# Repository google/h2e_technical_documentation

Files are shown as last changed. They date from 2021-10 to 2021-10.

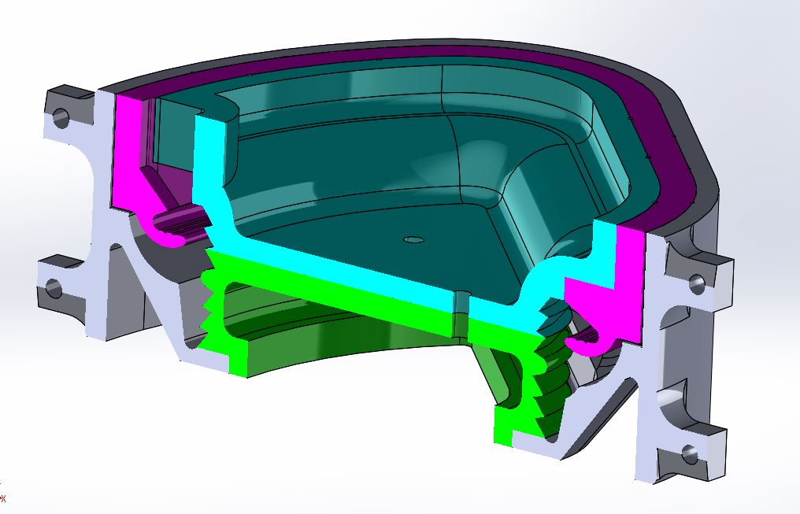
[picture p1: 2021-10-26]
CAD_files/P4-Grommets/P4-Pie-Shaped-Grommet/CrossSectionGromPieMold.JPG

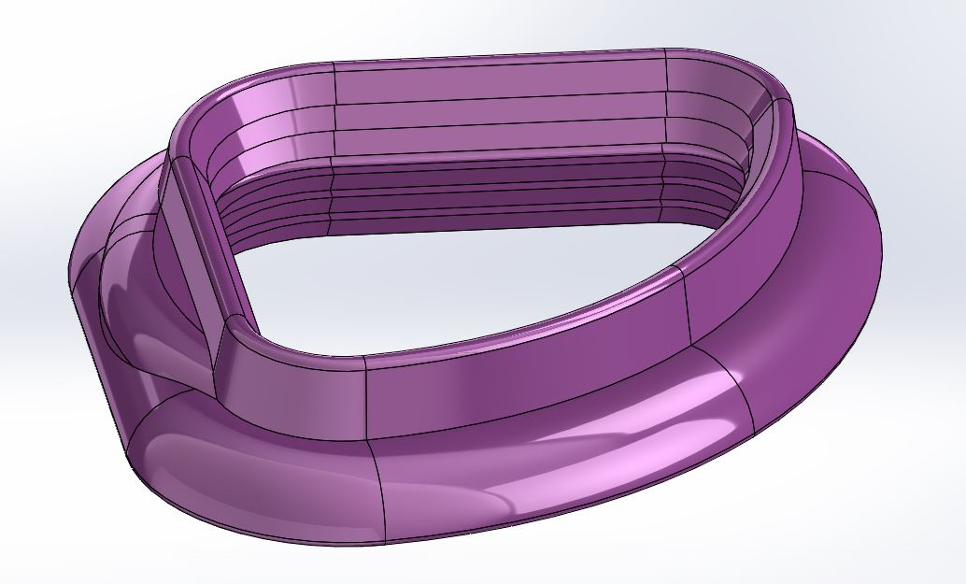
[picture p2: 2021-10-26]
CAD_files/P4-Grommets/P4-Pie-Shaped-Grommet/GromPie.JPG

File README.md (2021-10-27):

# H2E Technical Documentation Set

Summary:  
Over 2 billion people do not have access to safe drinking water. H2E was a 
project at X that aimed to tackle this challenge by creating a device that 
individual households could use to harvest water from the air. The team aimed 
to build a highly lightweight, portable, cheap (\<5% of user’s income) device 
that an individual could use to produce 5L of drinking water per day.

This is no longer an active project at X, so we are releasing our technical 
documents to allow others to build on our progress to date. To do so, we have 
made the following items public:

* [Nature paper](https://www.nature.com/articles/s41586-021-03900-w) with key 
findings
* Tools/code that enabled findings shared in the paper, and others in the AWH 
community can use, including:
    * “AWH-Geo” which can estimate the water output over time of any AWH 
    device. This can then be used to estimate the potential user base and 
    impact of an AWH device. On 
    [GitHub](https://github.com/AWH-GlobalPotential-X/AWH-Geo)
    * “JMP GeoProcessor” which uses geographic information systems (GIS) to 
    process the UNICEF/WHO data and join them to proper geographic boundaries. 
    In [FigShare](https://figshare.com/projects/AWH-GlobalPotential-X/96476) 
    * Much of the data analysis code used to produce the figures & charts in 
    the study. On [GitHub](https://github.com/AWH-GlobalPotential-X/AWH-Geo) 
* Two datasets on 
[FigShare](https://figshare.com/projects/AWH-GlobalPotential-X/96476) 
* Hardware assembly documentation
    * CAD files of our prototype device: These can be found in the folder 
    called “CAD_files” 
    * “Assembly_documentation.pdf”, this document details our prototype
    assembly process and learnings
* [Patent Non-Assertion Pledge ](https://storage.googleapis.com/x-prod.appspot.com/files/H2E%20Patent%20Non-Assertion%20Pledge.pdf)

Data and geospatial tools around access to safe drinking water are provided 
here to aid academic reproducibility and advancement in the context of the 
Nature Paper “Global Potential of Harvesting Drinking Water from Air using 
Solar Energy”. They should not be used for decision making without extensive 
validation. This caveat applies even more strongly outside the field of 
atmospheric water generation, where assumptions and approximations made may not 
be suitable . Users are encouraged to use the official public sources 
(primarily WHO/UNICEF JMP) from which they are derived.

Data and results capture a snapshot at the time of research, and are compiled 
at the time of publication (2021-10-27). They will not be updated, even as 
underlying realities change.

The prototype described here is a purely experimental device. While 
substitutions and modifications are reasonably straightforward, water harvested 
with this experimental device is not intended to be ingested. Among other design choices, adhesives were selected for experimental performance and would need to be substitued with ones meeting food grade standards. 

The views expressed in the paper and co-released documentation are the 
author’s, and not necessarily the views of authors’ employers.

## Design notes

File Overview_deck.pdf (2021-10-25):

Confidential & Proprietary

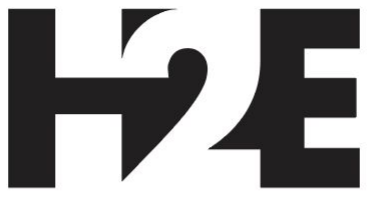
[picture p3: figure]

# Hydration to Everyone

Providing clean drinking water to every household without the need of treatment or transportation

# Problem: 2 bn people lack access to safe & reliable drinking water

## Safety

Diarrheal diseases due to unsafe drinking water is responsible for approximately 485,000 deaths a year¹

WHO estimates that it will take $203 billion in infrastructure investment to provide piped water to people currently underserved⁶

## Affordability

Water access is often far from the home; women and girls spend 200 million hours daily collecting water for their homes²

## Accessibility

# Solution: Atmospheric Water Harvesting

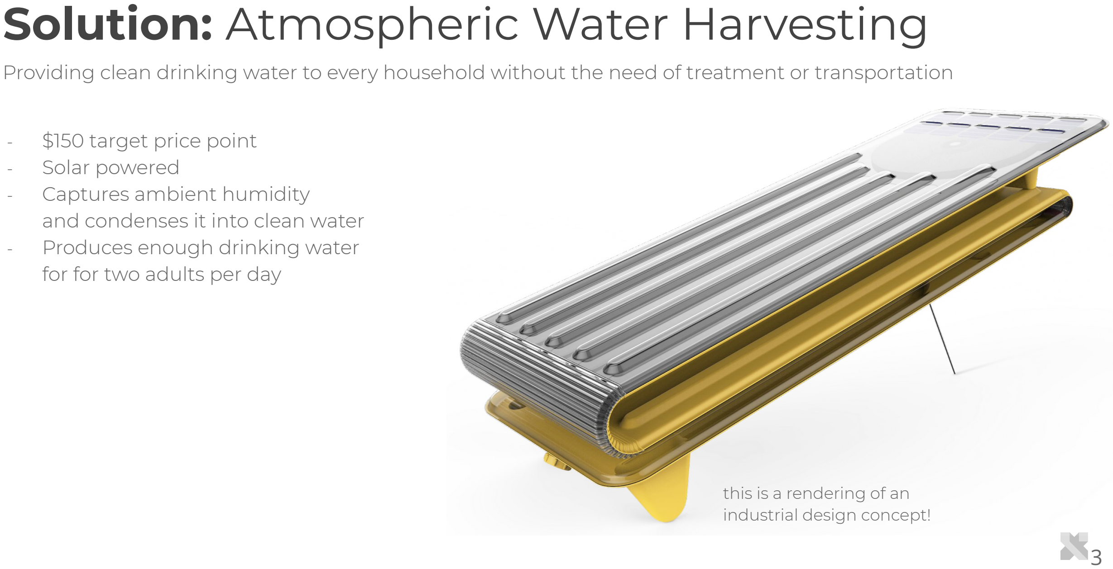
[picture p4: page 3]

### - $150 target price point - Solar powered - Captures ambient humidity and condenses it into clean water - Produces enough drinking water for for two adults per day

Providing clean drinking water to every household without the need of treatment or transportation

this is a rendering of an
industrial design concept!

## 1. Heating

## H2E’s Vacuum Formed Prototype

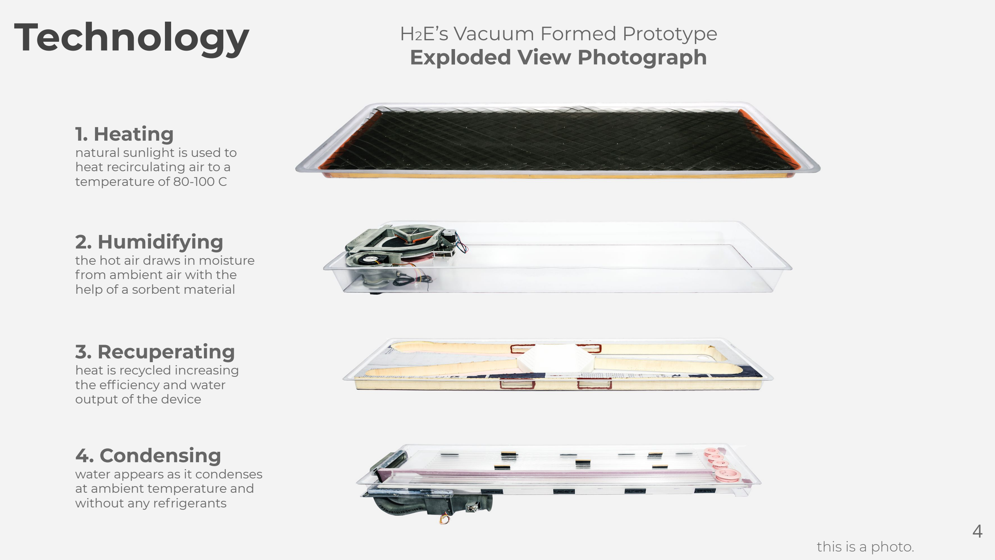
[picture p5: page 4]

natural sunlight is used to heat recirculating air to a temperature of 80-100 C

## Exploded View Photograph

## 2. Humidifying

the hot air draws in moisture from ambient air with the
help of a sorbent material

## 3. Recuperating

heat is recycled increasing the efficiency and water
output of the device

## 4. Condensing

water appears as it condenses at ambient temperature and without any refrigerants

this is a photo.

# Technology

# Air-Flow Path: Humidity supply

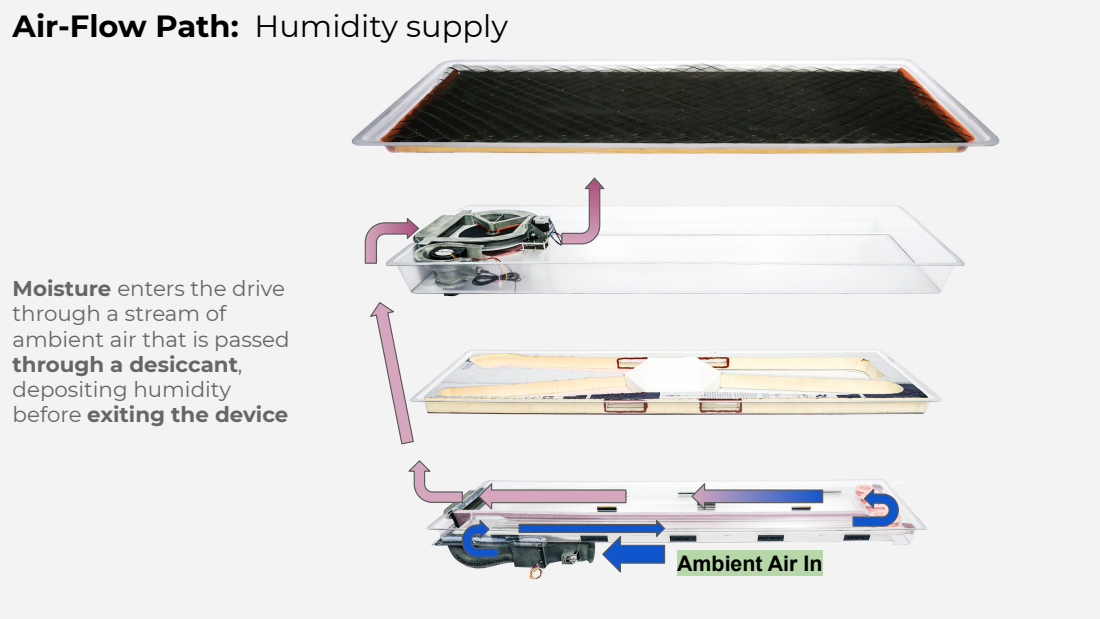
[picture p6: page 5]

Moisture enters the drive
through a stream of
ambient air that is passed
through a desiccant,
depositing humidity
before exiting the device

Ambient Air In

# Air-Flow Path: Recirculated Stream

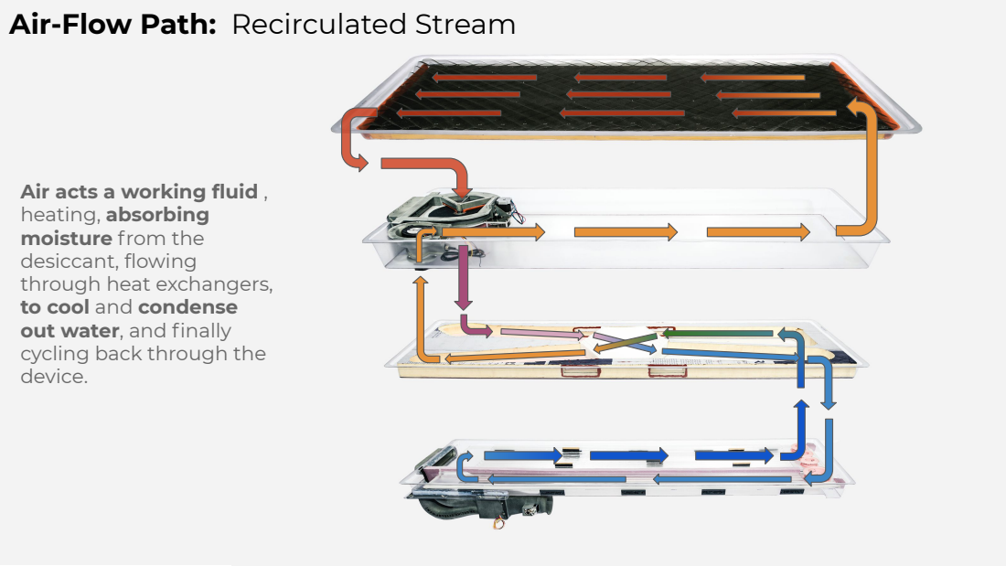
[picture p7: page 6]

Air acts a working fluid ,
heating, absorbing
moisture from the
desiccant, flowing
through heat exchangers,
to cool and condense
out water, and finally
cycling back through the
device.

# Photo of Appearance Mock without the Experimental Gear

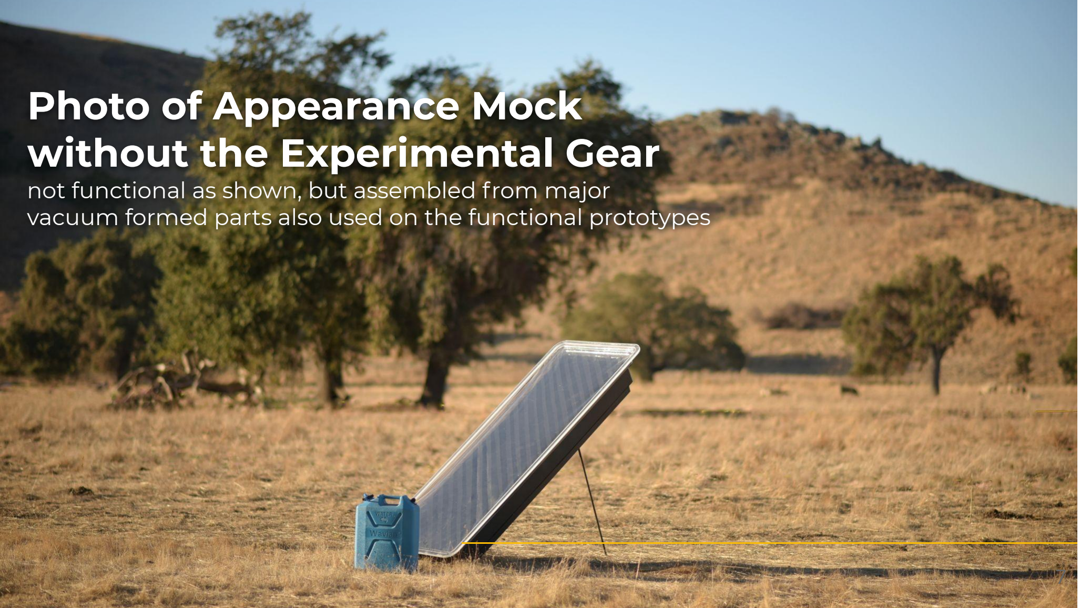
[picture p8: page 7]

## not functional as shown, but assembled from major vacuum formed parts also used on the functional prototypes

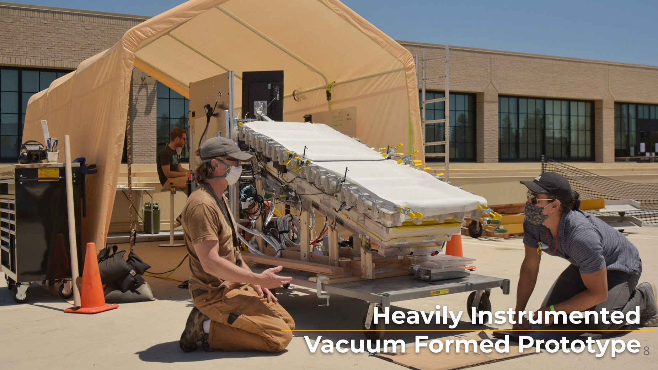
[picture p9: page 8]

# Heavily Instrumented Vacuum Formed Prototype

# Outdoor Experimental Results 2020

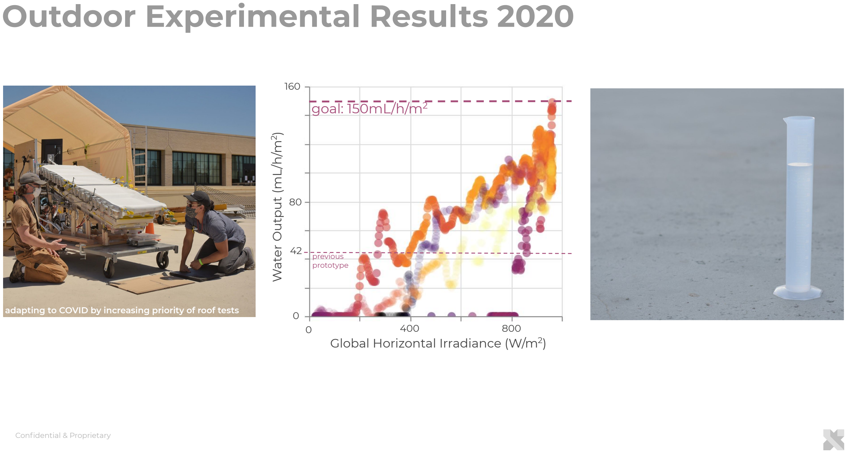
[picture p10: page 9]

Global Horizontal Irradiance (W/m² )

adapting to COVID by increasing priority of roof tests

previous
prototype

Water Output (mL/h/m2

)

42

0

160

80

0 | 400 | 800

goal: 150mL/h/m²

# Device Losses of an AWH

## Approximate Sankey Diagram of

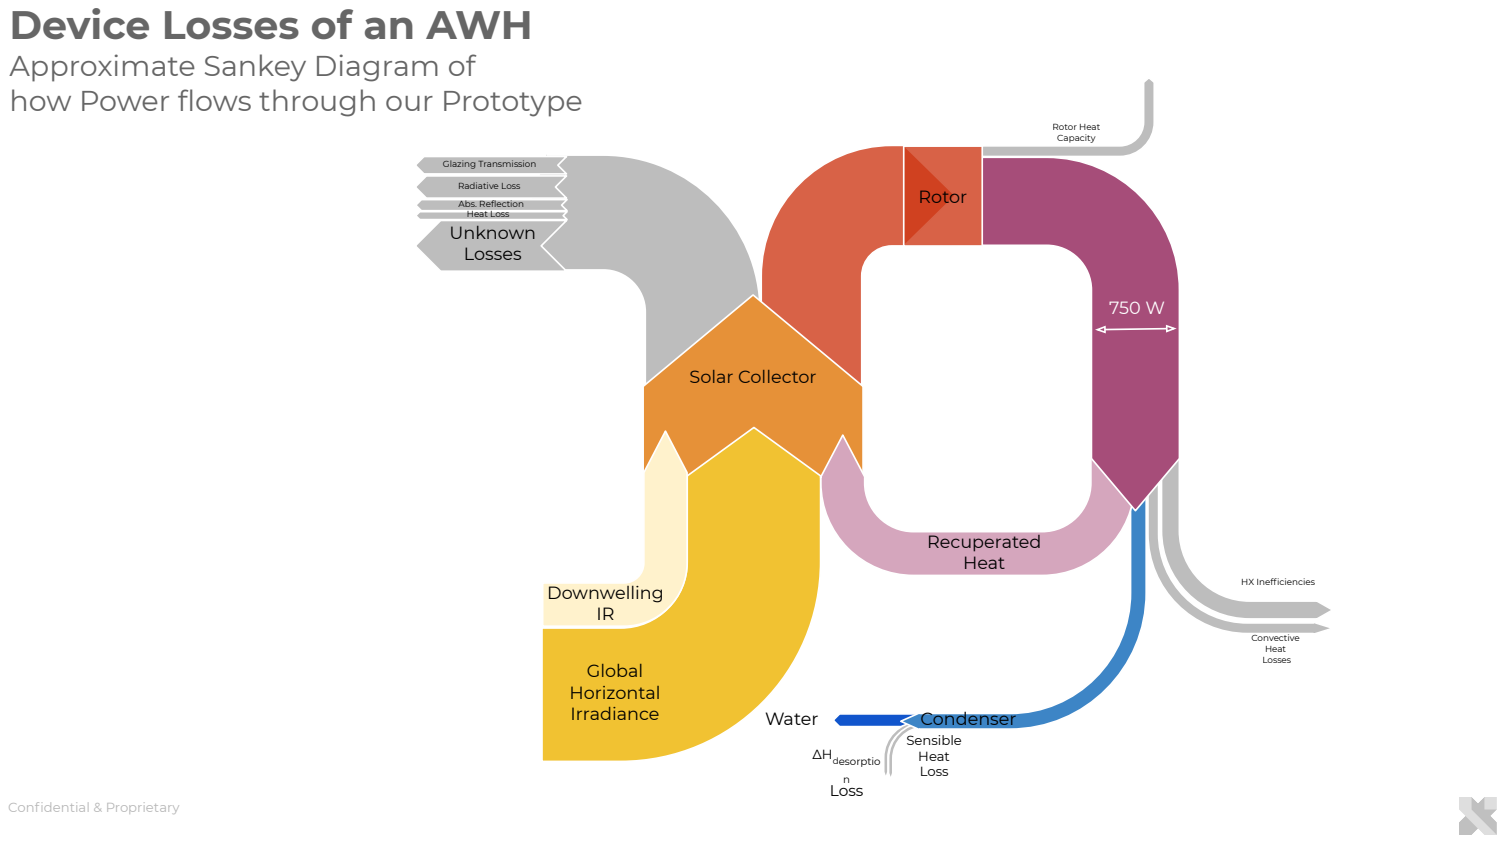
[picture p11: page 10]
Unknown Losses; Glazing Transmission; Radiative Loss; Abs. Reflection Heat Loss; Rotor; HX Inefficiencies; Convective Heat Losses; Water; Sensible Heat Loss; ∆Hdesorptio; n Loss; Condenser; Solar Collector; Global Horizontal Irradiance; Downwelling IR; Recuperated Heat; Rotor Heat Capacity

how Power flows through our Prototype

# Atmospheric Water Harvesting performs best where it is needed most

# Market

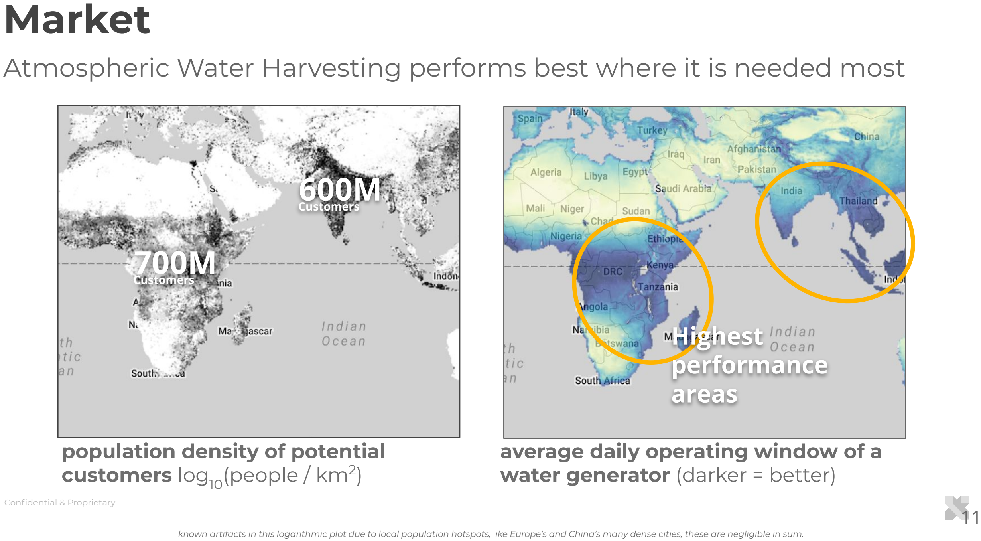
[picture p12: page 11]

known artifacts in this logarithmic plot due to local population hotspots, ike Europe’s and China’s many dense cities; these are negligible in sum.

## population density of potential customers log10(people / km²

)

## average daily operating window of a water generator (darker = better)

Customers

700M

Customers

600M

# Highest performance areas

# How AWH compares to other technologies

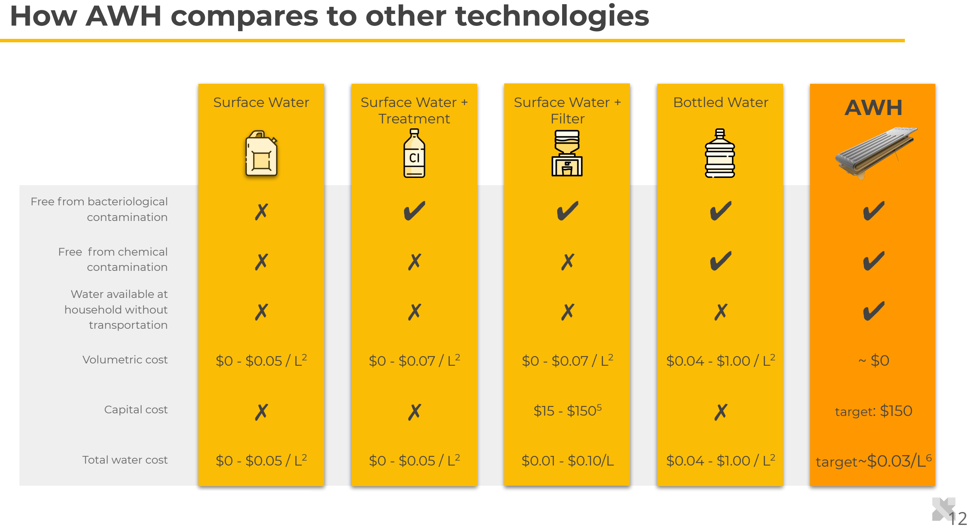
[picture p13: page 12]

Surface Water | Surface Water +
Treatment

Surface Water +
Filter
Bottled Water | AWH

Free from bacteriological
contamination | ✗ | ✔ | ✔ | ✔ | ✔

Free from chemical
contamination | ✗ | ✗ | ✗ | ✔ | ✔

Water available at
household without
transportation | ✗ | ✗ | ✗ | ✗ | ✔
Volumetric cost | $0 - $0.05 / L² | $0 - $0.07 / L² | $0 - $0.07 / L² | $0.04 - $1.00 / L² | ~ $0
Capital cost | ✗ | ✗ | $15 - $150⁵ | ✗ | target: $150
Total water cost | $0 - $0.05 / L² | $0 - $0.05 / L² | $0.01 - $0.10/L | $0.04 - $1.00 / L²

### target~$0.03/L⁶

# References

Page 9

1) Progress on household drinking water, sanitation and hygiene 2000-2017. Special focus on inequalities. New York: United Nations Children’s Fund (UNICEF) and World Health Organization, 2019.
2) Cook, J., P. Kimuyu, and D. Whittington (2016), The costs of coping with poor water supply in rural Kenya, Water Resources Research, 52, 841–859, doi:10.1002/2015WR017468.
3) End-User Preferences for and Performance of Competing POU Water Treatment Technologies among the Rural Poor of Kenya Jeff Albert, Jill Luoto, and David Levine Environmental Science & Technology 2010 44 (12), 4426-4432 DOI: 10.1021/es1000566
4) Low-end range: M. Dzodzomenyo, G. Fink, W. Dotse-Gborgbortsi, N. Wardrop, G. Aryeetey, N. Coleman, A. Hill, J. Wright; Sachet water quality and product registration: a cross-sectional study in Accra, Ghana. J Water Health 1 August 2018; 16 (4): 646–656. doi: https://doi.org/10.2166/wh.2018.055, High end: Data analysis from Ghana Living Standard Survey (GLSS7) 2017
5) PATH, Commercial approaches to delivering household water treatment and safe storage products and solutions to low-income households. Report 2012 https://path.azureedge.net/media/documents/TS_swp_perspectives_rpt.pdf
6) *Assuming 1500 L/yr x 3 yr and remineralization and/or chlorination for residual protection

Page 2
1) Prüss-Ustün A, Wolf J, Bartram J, et al. Burden of disease from inadequate water, sanitation and hygiene for selected adverse health outcomes: An updated analysis with a focus on low- and middle-income countries. Int J Hyg Environ Health. 2019;222(5):765-777. doi:10.1016/j.ijheh.2019.05.004
2) Collecting water is often a colossal waste of time for women and girls. UNICEF. (2021, October 15). Retrieved October 22, 2021, from
https://www.unicef.org/press-releases/unicef-collecting-water-often-colossal-waste-time-women-and-girls.
3) Hutton, Guy, Haller, Laurence & World Health Organization. Water, Sanitation and Health Team. ( 2004) . Evaluation of the costs and benefits of water and sanitation improvements at the global level / Guy Hutton and Laurence Haller. World Health Organization. https://apps.who.int/iris/handle/10665/68568

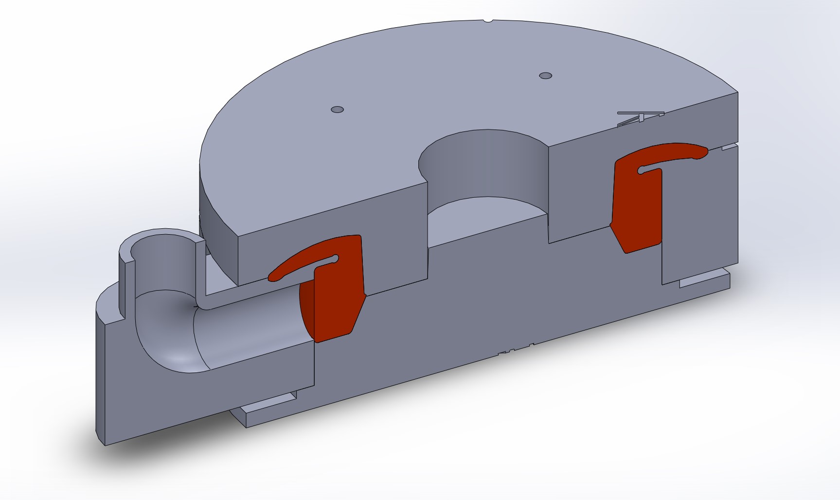
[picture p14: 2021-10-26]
CAD_files/P4-Grommets/Fan Grommet Mold.jpg

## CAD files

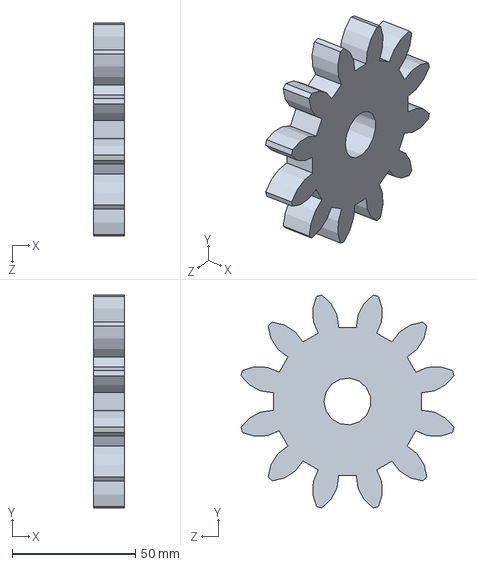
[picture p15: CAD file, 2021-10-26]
CAD_files/Complete P4 Full Assembly/P4_Full/spur gear_ai_P4Full.sldprt
12.7 x 86.4 x 86.4 mm

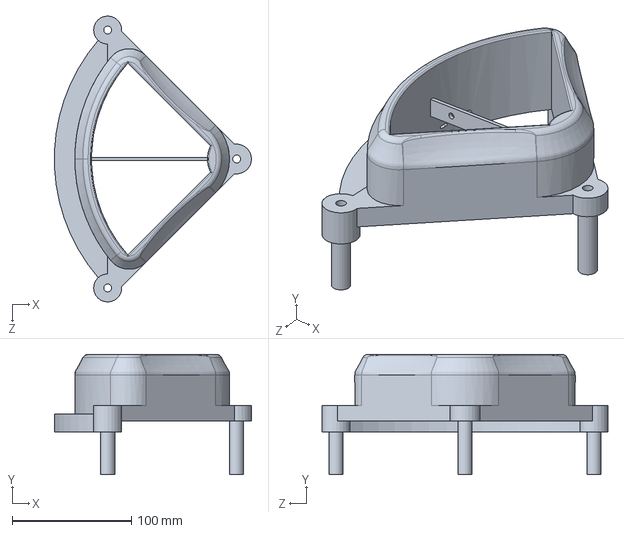
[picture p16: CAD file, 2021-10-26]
CAD_files/Complete P4 Full Assembly/P4_Full/BBP4_PiePieceBottom_P4Full.SLDPRT
165.3 x 101.0 x 240.0 mm

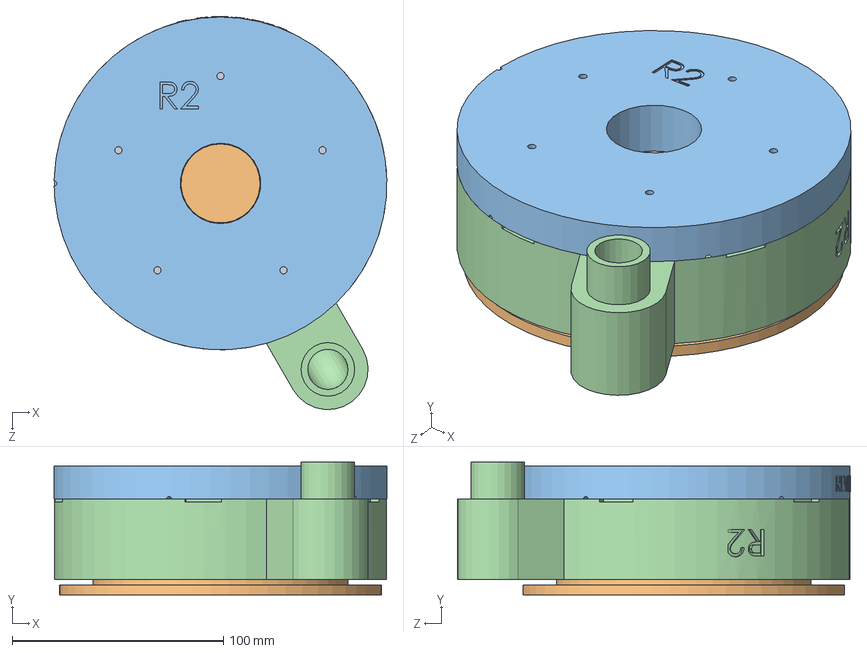
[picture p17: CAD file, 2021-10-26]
CAD_files/P4-Grommets/Fan Gromet Mold/Vent fan mold.SLDASM
157.4 x 62.8 x 186.0 mm
FAN grommet 2
Lower Core_fan_gromet_mold
Mold Lid
Mold Fan Grommet Lower Exterior

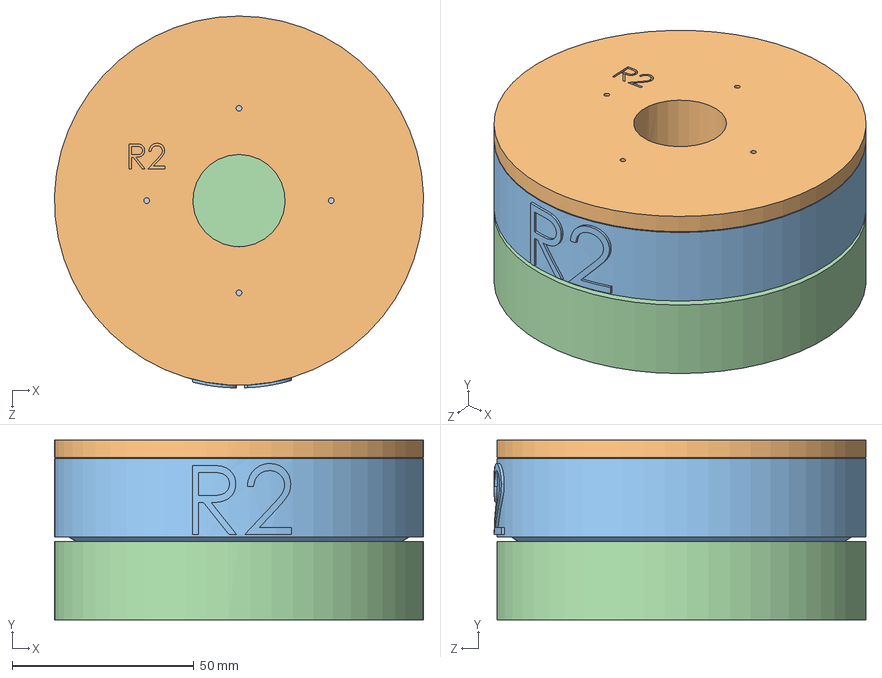
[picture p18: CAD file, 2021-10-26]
CAD_files/P4-Grommets/Gromzilla mold small port/Small port mold.SLDASM
101.6 x 49.5 x 102.4 mm
Rubber Port Tube
MoldHALF_A_small port
Center mold Small port
pass through mold Bottom side

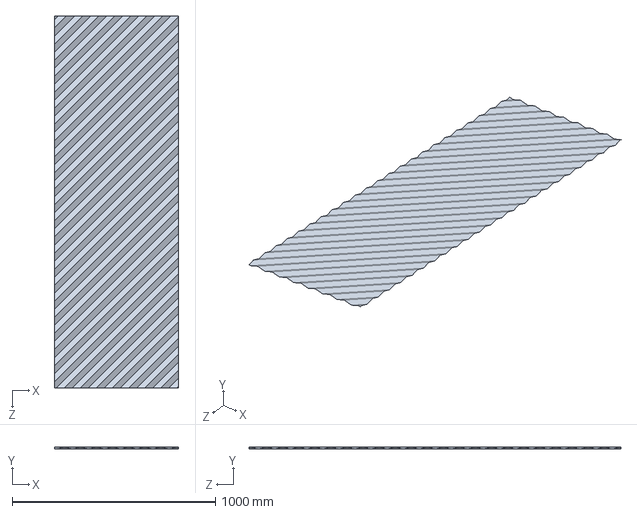
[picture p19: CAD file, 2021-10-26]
CAD_files/Complete P4 Full Assembly/P4_Full/T1 Sol Coat Mesh_P4Full.SLDPRT
609.6 x 11.2 x 1828.8 mm

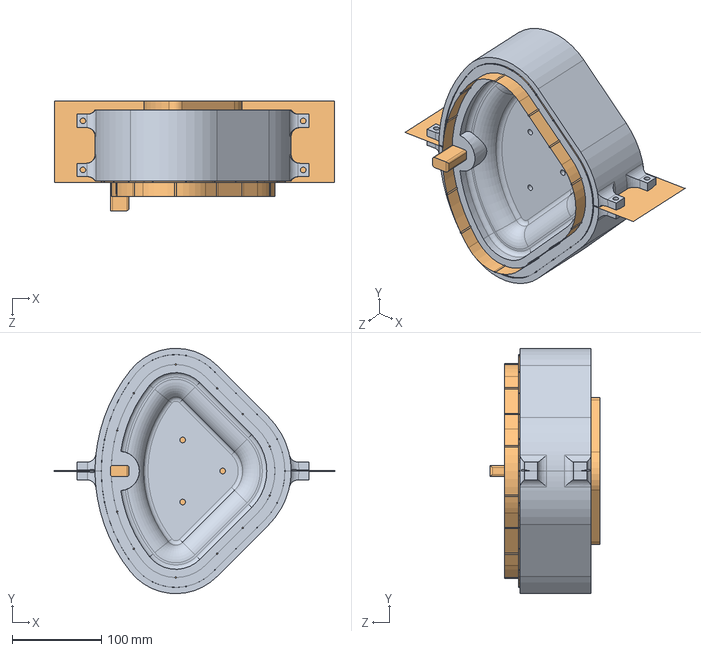
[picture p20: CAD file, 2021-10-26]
CAD_files/P4-Grommets/P4-Pie-Shaped-Grommet/P4-Pie-Shaped-Grommet/A_gromzillaP4MoldV2.SLDASM
314.0 x 275.1 x 122.8 mm
gromzillaP4MoldV2BodyV2
PosMold_GromzilPieV2

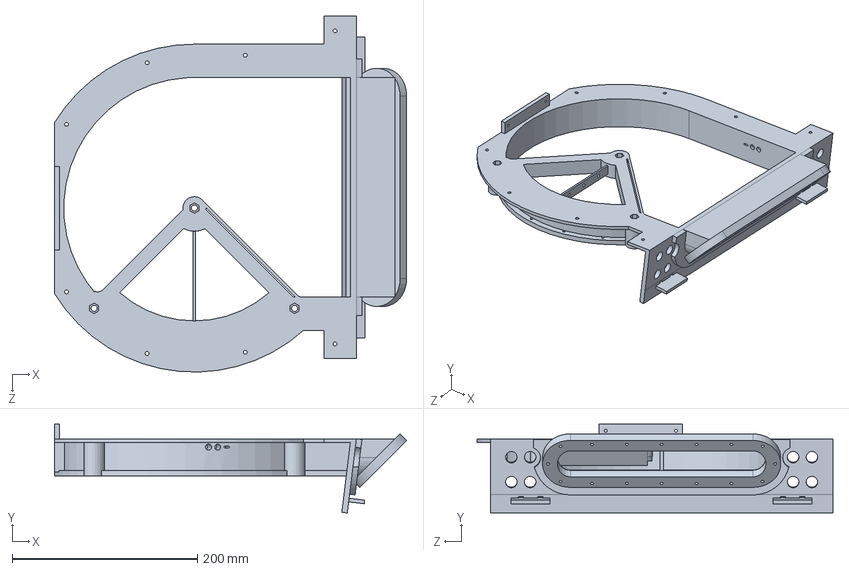
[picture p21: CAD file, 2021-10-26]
CAD_files/Complete P4 Full Assembly/P4_Full/BBP4_Shroud_Angle_For_FlowOp_P4Full.SLDPRT
380.3 x 96.1 x 384.3 mm

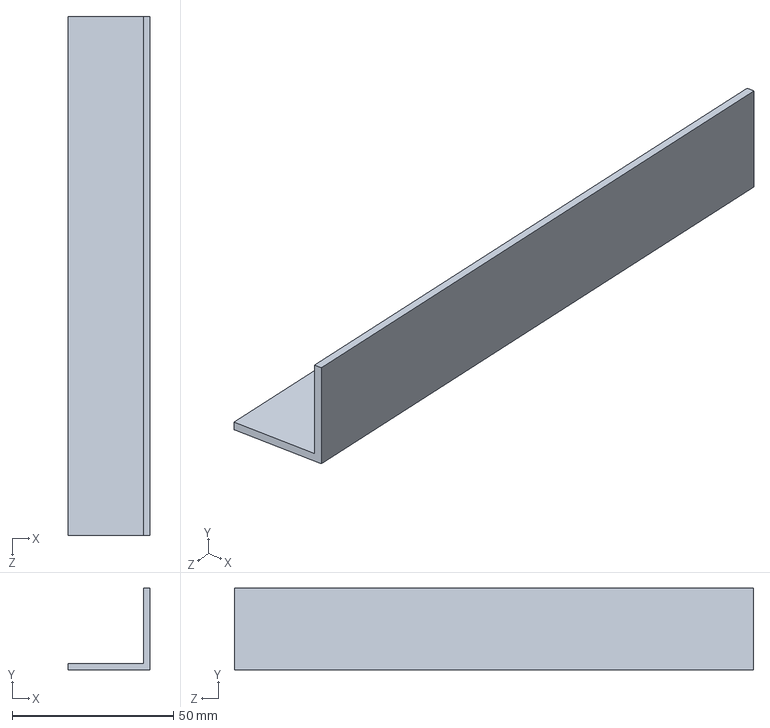
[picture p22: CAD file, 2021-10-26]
CAD_files/Complete P4 Full Assembly/P4_Full/Plastic Ell 1_P4Full.SLDPRT
25.4 x 25.4 x 161.0 mm

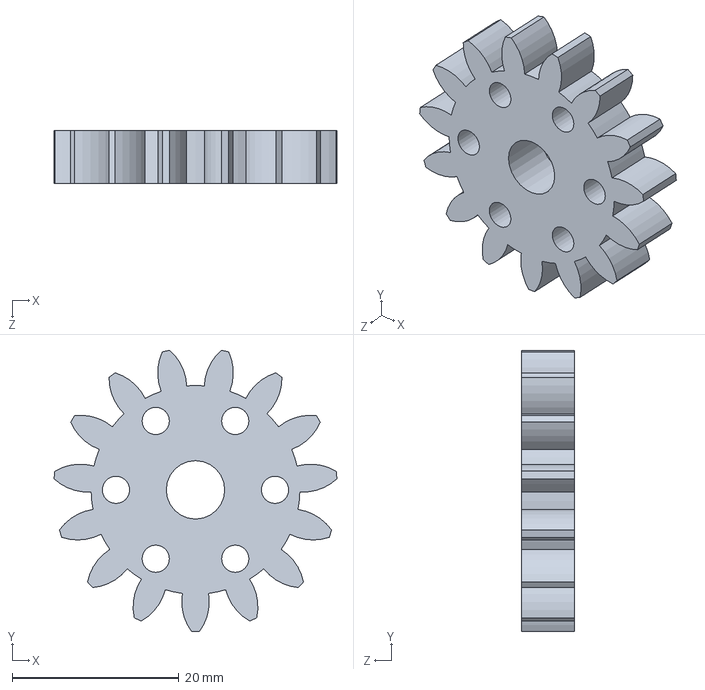
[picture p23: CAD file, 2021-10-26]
CAD_files/Complete P4 Full Assembly/P4_Full/P4_SmallGear_15T_M2_A20_P4Full.SLDPRT
33.9 x 33.7 x 6.35 mm

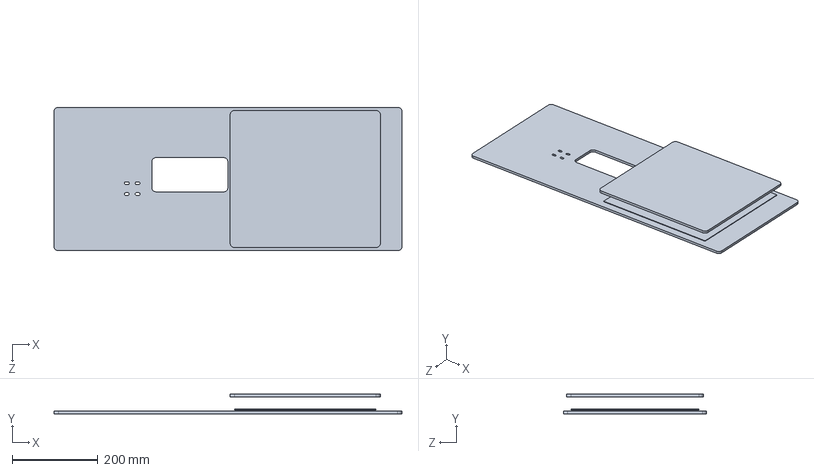
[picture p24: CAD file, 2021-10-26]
CAD_files/Complete P4 Full Assembly/P4_Full/WB_Housing_P4Full.SLDPRT
812.8 x 45.7 x 335.0 mm

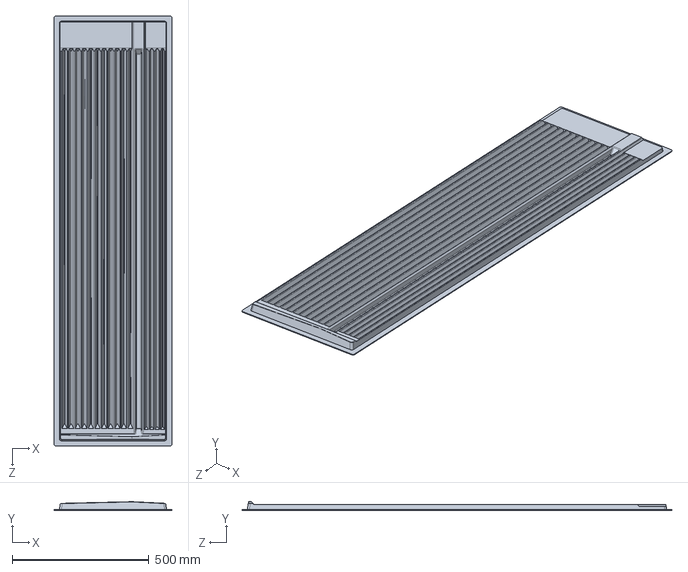
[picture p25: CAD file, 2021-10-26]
CAD_files/Complete P4 Full Assembly/P4_Full/Rib Clameshell #2 B_P4Full.SLDPRT
431.8 x 31.7 x 1574.8 mm

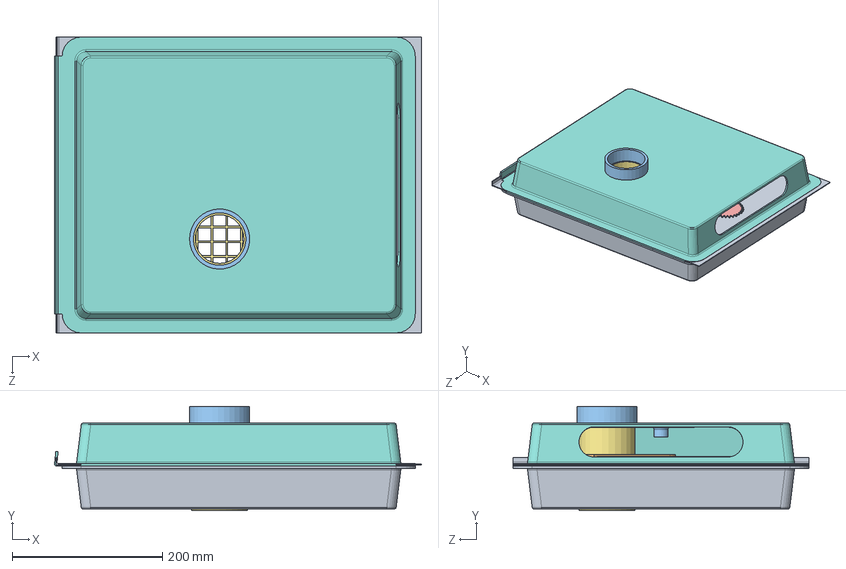
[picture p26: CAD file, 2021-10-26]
CAD_files/Complete P4 Full Assembly/P4_Full/Desicant wheel Assembly_P4Full.SLDASM
488.3 x 138.7 x 393.7 mm
FLAT PIE x 2
Wheel base plate
Wheel base plate MOTOR MOUNT
30 tooth gear
Stepper motor bracket
DummyWheelNick
Exhaust Plenum
intake_Plenum

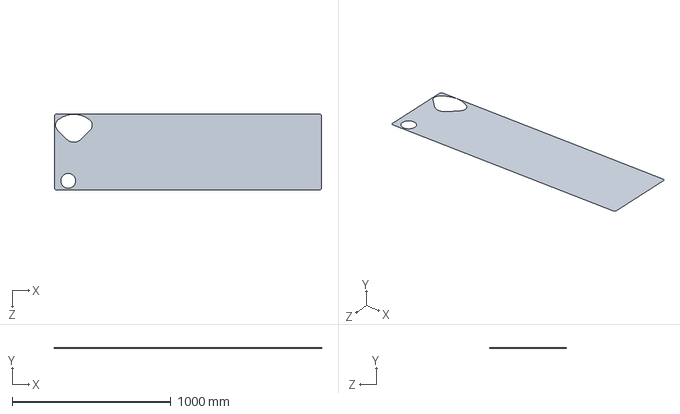
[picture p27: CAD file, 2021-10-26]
CAD_files/Complete P4 Full Assembly/P4_Full/T3 Mylar_P4Full.SLDPRT
1682.4 x 0.005 x 479.2 mm

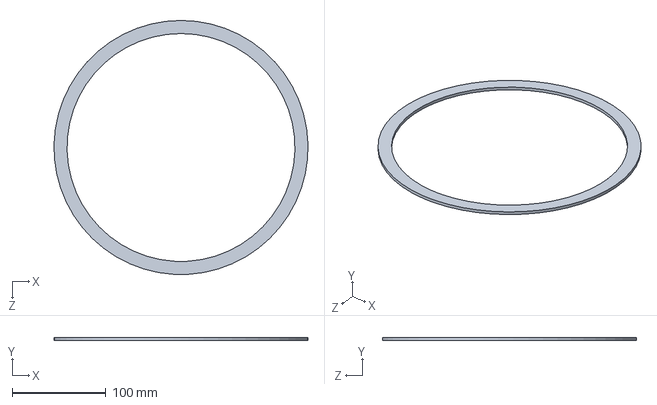
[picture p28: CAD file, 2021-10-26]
CAD_files/Complete P4 Full Assembly/P4_Full/BB4_smoothrimtopper_P4Full.SLDPRT
271.4 x 3.17 x 271.5 mm

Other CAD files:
CAD_files/Complete P4 Full Assembly/P4_Full/MASTER SKETCH_P4Full.SLDPRT
CAD_files/Complete P4 Full Assembly/P4_Full/TOPA_BBP4_V2_P4Full.SLDASM
CAD_files/Complete P4 Full Assembly/P4_Full/TRIPPLE GROMET SILICONE_P4Full.SLDPRT
CAD_files/Complete P4 Full Assembly/P4_Full/quarter D shaft_P4Full.SLDPRT
CAD_files/Complete P4 Full Assembly/P4_Full/132Fan_P4Full.SLDPRT
CAD_files/Complete P4 Full Assembly/P4_Full/1434K430_LIGHT DTY TWO-BOLT FLANGE-MOUNTED ROLLER BRNG_P4Full.SLDPRT
CAD_files/Complete P4 Full Assembly/P4_Full/1939K920_DC EQUIPMENT COOLING FAN_P4Full.SLDPRT
CAD_files/Complete P4 Full Assembly/P4_Full/30 tooth gear_P4Full.SLDPRT
CAD_files/Complete P4 Full Assembly/P4_Full/47065T253_ALUMINUM T-SLOTTED FRAMING EXTRUSION_P4Full.SLDPRT
CAD_files/Complete P4 Full Assembly/P4_Full/5012K482_AIR AND WATER QUICK-DISCONNECT TUBE COUPLING_P4Full.SLDPRT
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
